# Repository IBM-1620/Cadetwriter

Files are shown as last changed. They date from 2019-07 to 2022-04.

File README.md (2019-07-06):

# Cadetwriter
Developed as a by-product of the IBM 1620 Jr. project, the Cadetwriter is a general-purpose ASCII terminal.  It can be connected via RS-232 or USB to any mini, micro, mainframe, or replica computer as a terminal device.  A commercial quality IBM/Lexmark Wheelwriter 1000 was adapted by interposing a circuit board containing a Teensy 3.5 microcontroller between the typewriter's keyboard and motherboard.  Custom firmware controls the typewriter and communicates with the host computer.  To support the full ASCII character set, characters not on the printwheel are synthesized using overprinted characters and "period graphics".  The Cadetwriter can print up to 16cps and is a reliable, low-maintenance, low-cost substitute for Teletype, DECwriter, Diablo, Spinwriter, Imagewriter, etc. teleprinters.

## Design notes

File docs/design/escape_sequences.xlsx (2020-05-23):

Cadetwriter Escape Sequence Recognition
Type | Escape (1 char) | Opener (1 char) | Parameters (0 - n chars) | Intermediates (0 - n chars) | Final (1 char)
CSI | <esc> 0x1B | [ 0x5B | 0123456789:;<=>? 0x30 - 0x3F | <space>!"#$%&'()*+,-./ 0x20 - 0x2F | @ABCDEFGHIJKLMNOPQRSTUVWXYZ[\]^_ `abcdefghijklmnopqrstuvwxyz{|}~ 0x40 - 0x7E
Function | <esc> 0x1B |  |  | <space>!"#$%&'()*+,-./ 0x20 - 0x2F | 0123456789:;<=>? @ABCDEFGHIJKLMNOPQRSTUVWXYZ[\]^_ `abcdefghijklmnopqrstuvwxyz{|}~ 0x30 - 0x7E
Type | Escape (1 char) | Opener (1 char) | Strings (0 - n chars) |  | Final (1 char)
String | <esc> 0x1B | PX]^_ 0x50, 0x58, 0x5D, 0x5E, 0x5F | <bs><tab><lf><vt><ff><cr> <space>!"#$%&'()*+,-./0123456789:;<=>? @ABCDEFGHIJKLMNOPQRSTUVWXYZ[\]^_ `abcdefghijklmnopqrstuvwxyz{|}~ 0x08 - 0x0D, 0x20 - 0x7E |  | <esc> \ 0x1B & 0x5C <bel> 0x07
Special cases:
 | NUL (0x00) and DEL (0x7F) are always ignored.
 | CAN (0x18) and SUB (0x1A) immediately abort the sequence.
 | All control characters (0x01 - 0x1F) except CAN (0x18), SUB (0x1A), and ESC (0x1B) anywhere, except in String bodies, perform their normal action.
 | P (0x50), X (0x58), ] (0x5D), ^ (0x5E), and _ (0x5F) cannot be used to terminate Function sequences unless they contain at least one Intermediate character.
 | Any ESC (0x1B) after the first, except in Strings, immediately aborts the current sequence and starts another one.

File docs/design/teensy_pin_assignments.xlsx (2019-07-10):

Teensy Pin Assignments
Pins | Port | Bit | I/O | Name | Firmware (1.7) | Firmware (2.0)
0 | B | 16 | I | RXD0, RX1 | UART_RX | UART_RX
1 | B | 17 | O | TXD0, TX1 | UART_TX | UART_TX
2 | D | 0 | I |  | ROW_IN_0 | ROW_IN_0
3 | A | 12 | I |  | COL_10 | COL_10
4 | A | 13 | I |  | COL_11 | COL_11
5 | D | 7 | I |  | ROW_IN_7 | ROW_IN_7
6 | D | 4 | I |  | ROW_IN_4 | ROW_IN_4
7 | D | 2 | I | RXD2, RX3 | ROW_IN_2 | ROW_IN_2
8 | D | 3 | I | TXD2, TX3 | ROW_IN_3 | ROW_IN_3
9 | C | 3 | I | RXD1, RX2 | COL_3 | COL_3
10 | C | 4 | I | TXD1, TX2, SS | COL_6 | COL_6
11 | C | 6 | I | MOSI | COL_7 | COL_7
12 | C | 7 | I | MISO | COL_8 | COL_8
13 | C | 5 | O | LED_BUILTIN | ORANGE_LED | ORANGE_LED
14 | D | 1 | I | ADC0, A0 | ROW_IN_1 | ROW_IN_1
15 | C | 0 | I | ADC1, A1 | COL_4 | COL_4
16 | B | 0 | O | ADC2, A2 | ROW_OUT_0 | ROW_OUT_0
17 | B | 1 | O | ADC3, A3 | ROW_OUT_1 | ROW_OUT_1
18 | B | 3 | O | ADC4, A4, SDA0, SDA | ROW_OUT_3 | SERIAL_CTSX
19 | B | 2 | O | ADC5, A5, SCL0, SCL | ROW_OUT_2 | SERIAL_RTSX
20 | D | 5 | I | ADC6, A6 | ROW_IN_5 | ROW_IN_5
21 | D | 6 | I | ADC7, A7 | ROW_IN_6 | ROW_IN_6
22 | C | 1 | I | ADC8, A8 | COL_14 | COL_14
23 | C | 2 | I | ADC9, A9 | COL_1 | COL_1
24 | E | 26 | I |  | JUMPER_6 | JUMPER_6
25 | A | 5 | I |  |  | COL_??
26 | A | 14 | I |  | COL_12 | COL_12
27 | A | 15 | I |  | COL_13 | COL_13
28 | A | 16 | I |  | COL_2 | COL_2
29 | B | 18 | O |  | ROW_OUT_6 | ROW_OUT_6
30 | B | 19 | O |  | ROW_OUT_7 | ROW_OUT_7
31 | B | 10 | O | ADC12, A12, RXD3, RX4 | ROW_OUT_4 | ROW_OUT_4
32 | B | 11 | O | ADC13, A13, TXD3, TX4 | ROW_OUT_5 | ROW_OUT_5
33 | E | 24 | O | ADC14, A14, TXD4, TX5 | BLUE_LED | BLUE_LED
34 | E | 25 | I | ADC15, A15, RXD4, RX5 | JUMPER_7 | JUMPER_7
35 | C | 8 | I | ADC16, A16 | COL_9 | COL_9
36 | C | 9 | O | ADC17, A17 | ROW_ENABLE | ROW_ENABLE
37 | C | 10 | O | ADC18, A18, SCL1 | SERIAL_RTS | ROW_OUT_2X
38 | C | 11 | I | ADC19, A19, SDA1 | SERIAL_CTS | ROW_OUT_3X
39 | A | 17 | I | ADC20, A20 | COL_5 | COL_5
40 | A | 28
41 | A | 29
42 | A | 26
43 | B | 20
44 | B | 22
45 | B | 23
46 | B | 21
47 | D | 8 |  | RX6
48 | D | 9 |  | TX6
49 | B | 4 |  | ADC23, A23
50 | B | 5 |  | ADC24, A24
51 | D | 14
52 | D | 13
53 | D | 12
54 | D | 15
55 | D | 11
56 | E | 10
57 | E | 11
58 | E | 0
59 | E | 1
60 | E | 2
61 | E | 3
62 | E | 4
63 | E | 5
64 |  |  |  | ADC10, A10
65 |  |  |  | ADC11, A11
66 |  |  |  | ADC21, A21, DAC0
67 |  |  |  | ADC22, A22, DAC1
68 |  |  |  | ADC25, A25
69 |  |  |  | ADC26, A26
 |  |  |  |  | input
 |  |  |  |  | output

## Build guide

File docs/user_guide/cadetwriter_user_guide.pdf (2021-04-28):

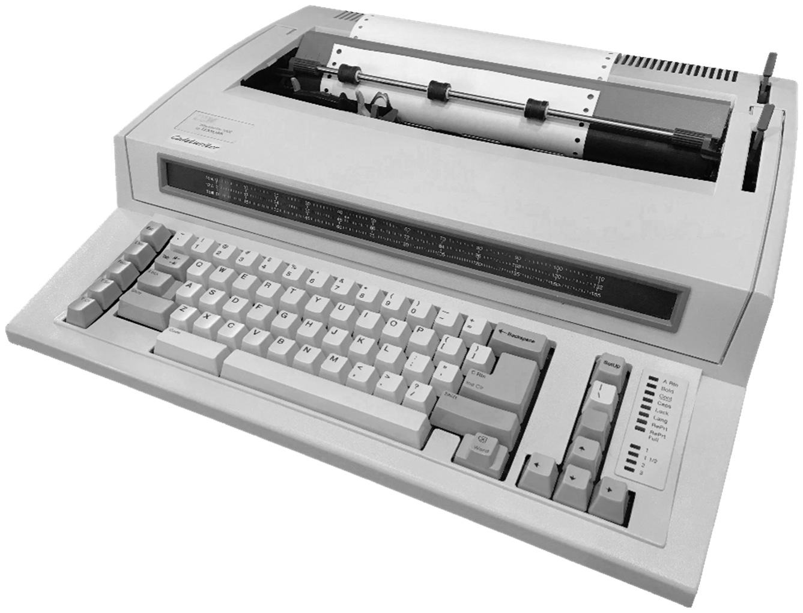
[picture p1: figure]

# Cadetwriter

# (ASCII Terminal)

# User Guide

### IBM 1620 Jr. Team Computer History Museum Revision 1.01 – April 2021

2

## Contents

3

4

## 1. Introduction

This guide describes the operation of Cadetwriter, a Wheelwriter‐based computer terminal. It is an extension of the console typewriter created for the Computer History Museum’s IBM 1620 Jr. project. Its complete design, assembly instructions, and firmware are available, free of charge from: https://github.com/IBM‐1620/Cadetwriter.

### 1.1 Description

Cadetwriter is a general‐purpose, ASCII computer teleprinter similar to a Teletype, DECwriter, Flexowriter, or IBM 2741 terminal. It can be used as an input/output device connected to any computer ‐ old, new, or replica ‐ with an RS‐232 or USB interface. It can also be operated as a stand‐alone typewriter by changing a hardware jumper.
Cadetwriter is built by installing a custom serial interface board inside an IBM/Lexmark Wheelwriter 1000 electronic typewriter.¹
Firmware in this
board’s ARM processor reads the keyboard, controls the printer, and communicates with the computer.

### 1.2 Features

Cadetwriter has the following features:

- Print speed up to 16 or 20 characters per second, depending on Wheelwriter model.
- 10, 12, or 15 pitch interchangeable typewheels, multiple fonts.²
- 80 ‐ 198 characters per line depending on printwheel pitch and carriage width.
- Standard and wide carriage widths.
- Full ASCII character set.
- RS‐232 and USB interfaces.
- Full or half duplex.
- Baud rates: 50, 75, 110, 134, 150, 200, 300, 600, 1200, 1800, 2400, 4800, 9600, 19200, 38400, 57600, 76800, 115200, or 230400.
- None, odd, or even parity.
- 7 or 8 data bits.

1 Although Cadetwriter was created using a Wheelwriter 1000, other model Wheelwriters also work with little or no change to the firmware or serial interface board. 2 Cadetwriter output is optimized for the Courier 10 ASCII (#1353909) and

Artisan 10 (#1353520) printwheels.

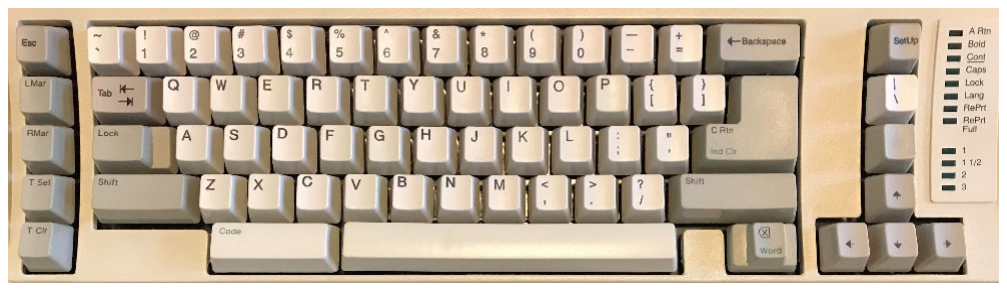
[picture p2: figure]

5

- 1 or 2 stop bits.
- Hardware (RTS/CTS or RTR/CTS) and/or software (XON/XOFF) flow control.
- Uppercase/lowercase or uppercase only.
- End‐of‐line: CR, LF, CR/LF, or LF/CR.
- Adjustable left and right margins.
- Settable tab stops.
- All settings are permanently retained.³

### 1.3 Keyboard

The Cadetwriter keyboard is as close to a typical ASCII terminal layout as possible with the Wheelwriter typewriter. In addition to printable characters, the keyboard includes keys to set/clear margins and tabs, move the carriage, and enter SetUp mode. The “Code” key functions as the “Ctrl” (control) key. This is Cadetwriter’s keyboard using replacement ASCII keycaps:

### 1.4 Printer

The printer in Cadetwriter is a Daisy wheel mechanism which prints fully‐ formed characters. Many printwheels exist for the Wheelwriter typewriter with different fonts, pitches, and foreign languages. Most of them contain a “typewriter” set of print characters which includes ½, ¼, ¢, ±, °, ², ³, §, and ¶. Missing are the ASCII characters <, >, \, ^, `, {, |, }, and ~.

IBM/Lexmark produced a limited number of special “ASCII” printwheels with all of the ASCII characters, but they are rare and hard to find. These are the preferred ones to use with Cadetwriter as they produce the best‐looking output and print at maximum speed. Here is Cadetwriter’s full character set when using the Courier 10 ASCII printwheel (#1353909):

3 Wheelwriter settings are stored in volatile memory, preserved by battery backup. All Cadetwriter setting are stored in non‐volatile EEPROM.

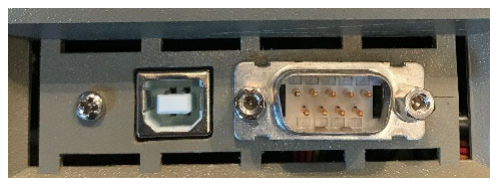
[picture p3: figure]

6

When using a standard, non‐ASCII printwheel, Cadetwriter synthesizes the missing characters by overprinting available characters, or “period graphic” characters⁴
, or a combination of the two methods. Composite characters, due to their complexity, take longer to print than the native ones, reducing the effective print speed. Here is the full ASCII character set as printed by Cadetwriter using the Artisan 10 printwheel (#1353520):

### 1.5 Indicator Lights

In normal operation, only the single‐spacing indicator light will be on. However, after printing several pages of output, the “RePrt Full” will light up, but will not affect the operation of the terminal.

The Shift Lock key on the keyboard functions as a caps lock, but the “Lock” indicator will not light up. This is due to the way Cadetwriter interfaces with the Wheelwriter electronics.

Note that when operating as a stand‐alone Wheelwriter typewriter, all of the indicator lights will have their standard meaning.

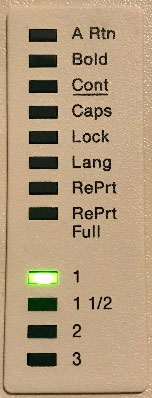
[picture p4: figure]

### 1.6 Serial Ports

Cadetwriter has two serial ports for connecting to a computer – RS‐232 and USB. The RS‐232 port is a male
DE‐9 (DTE) connector. The interface
uses RS‐232 voltages, not TTL level.
The USB port is a standard Type B receptable. Which port is used and its communication parameters are specified in the configuration settings [see section 2.2].

4 Period graphic characters are formed by a combination of micro‐space carriage movements (up, down, left, and right) and printing periods.

7

### The DE-9 pin assignments are:

Pin | Signal
1 | DCD – Data Carrier Detect †
2 | RXD – Received Data
3 | TXD – Transmitted Data
4 | DTR – Data Terminal Ready †
5 | GND – Common Ground
6 | DSR – Data Set Ready †
7 | RTS – Request To Send / RTR – Ready To Receive
8 | CTS – Clear To Send
9 | RI – Ring Indicator †

† DTR and DSR are not active and are connected together. DCD and RI are not connected.

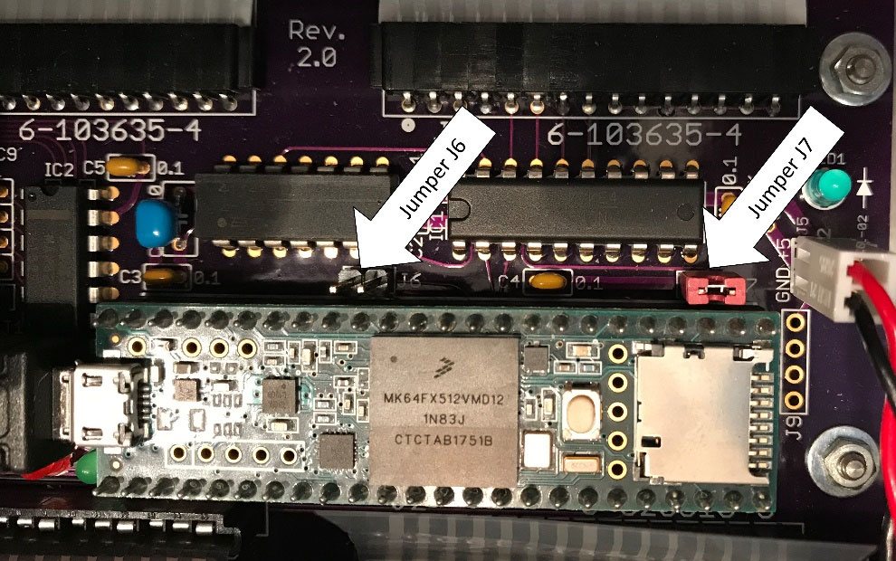
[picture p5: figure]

8

## 2. Setup

When connecting Cadetwriter to a computer for the first time, a little setup is required.

### 2.1 Selecting the Emulation

Four emulations are available by setting hardware jumpers on the serial interface board:

J6 Jumper | J7 Jumper | Emulation
| | IBM 1620 Jr. Console Typewriter
| installed | Cadetwriter ASCII Terminal
installed | | <available for future emulation>
installed | installed | Standalone Wheelwriter Typewriter
Here are the jumpers set to Cadetwriter ASCII Terminal emulation:

The emulation jumpers are tested only once when Cadetwriter is turned on. They can be changed when the device is off or on, but only take effect the next time it is turned on.

### 2.2 Batteries

It is recommended that you do NOT install batteries in Cadetwriter. When batteries are installed, it is possible for the Cadetwriter firmware to get out of sync with the typewriter settings, causing faulty operation. When batteries are not installed and the batteries installed configuration setting is

9

false, the firmware will set all typewriter settings to a known state at power on and operate correctly.

### 2.3 Configuring Cadetwriter

Most of the operations of Cadetwriter can be controlled by firmware configuration settings. These values are set interactively via a sequence of queries and controlled responses when in SetUp mode. The settings are effective for as long as Cadetwriter is turned on and can be optionally stored in EEPROM for persistence.

SetUp mode is entered by holding the “Code” and then pressing the “SetUp” key. The “SetUp” key is ignored if not used with the “Code” key. SetUp mode is not available when Cadetwriter is jumpered to be a standalone Wheelwriter typewriter.

While in SetUp mode, no data is sent to the computer and flow control (if enabled in settings) is asserted so that data should not be sent by the computer. If data is received, it will not be processed until SetUp mode is exited and may be lost if communication settings are changed.

SetUp mode starts by printing the following header which reports the emulation selected and the revision number of the firmware.

Next, the following command query is printed:

This illustrates the consistent way that SetUp mode queries commands and non‐typewriter settings:
- “Command” or the name of a specific setting (e.g., parity) is printed first.
- Next, all valid responses are shown inside brackets, separated by “/”s.⁵
- For commands, the default option is printed in all uppercase. All other possible commands are in lowercase.
- For settings, the current value [default] of the setting is printed in all uppercase. All other possible responses are in lowercase.

5 The exceptions are the baud rate, line length, and line offset settings which print the supported range of values and the current [default] value within the brackets. For example: “baud rate [50‐230400, 1200]”.

10

- The print mechanism spaces to the right so that the entire query is viewable.
- The user now enters a response to the query. Responses are case‐ insensitive. Only enough characters to uniquely specify a value need to be typed. In most cases, the first character is sufficient. If an invalid character is typed, nothing prints and the terminal beeps.
- Once enough characters are entered to uniquely identify the response, the remaining characters of it are printed and SetUp mode executes the command or updates the setting and moves on to the next one.
- When responding to the line length and line offset settings, a carriage return terminates the value.
- If only a carriage return is entered, then the default response is used. For commands, this exits SetUp mode. For settings, this retains the current value.
- At the end of all settings, SetUp mode asks if the new settings should be saved in EEPROM.

If “yes”, all settings are preserved until changed. If "no”, the new settings are in effect only as long as Cadetwriter remains turned on.

There are five commands:

settings ‐ Interactively review and optionally change all firmware configuration settings. See section 3 of this guide for details.

errors ‐ Print all errors and warnings that have occurred since the last power on or reset. Optionally, the error and warning counters can be cleared.

character set ‐ Print the full character set.

typewriter ‐ Set or clear all relevant typewriter settings. See section 4 of this guide for details.

quit ‐ End SetUp mode.

It is also possible to reset all firmware configuration settings to their “factory” default by pressing the “Shift”, “Code”, and “SetUp” keys together, aka Shift‐Ctrl‐SetUp. After resetting the settings, the firmware will re‐ establish all margins & tab stops and a confirmation message will be printed.

11

When using the RS‐232 serial port, the default settings are:

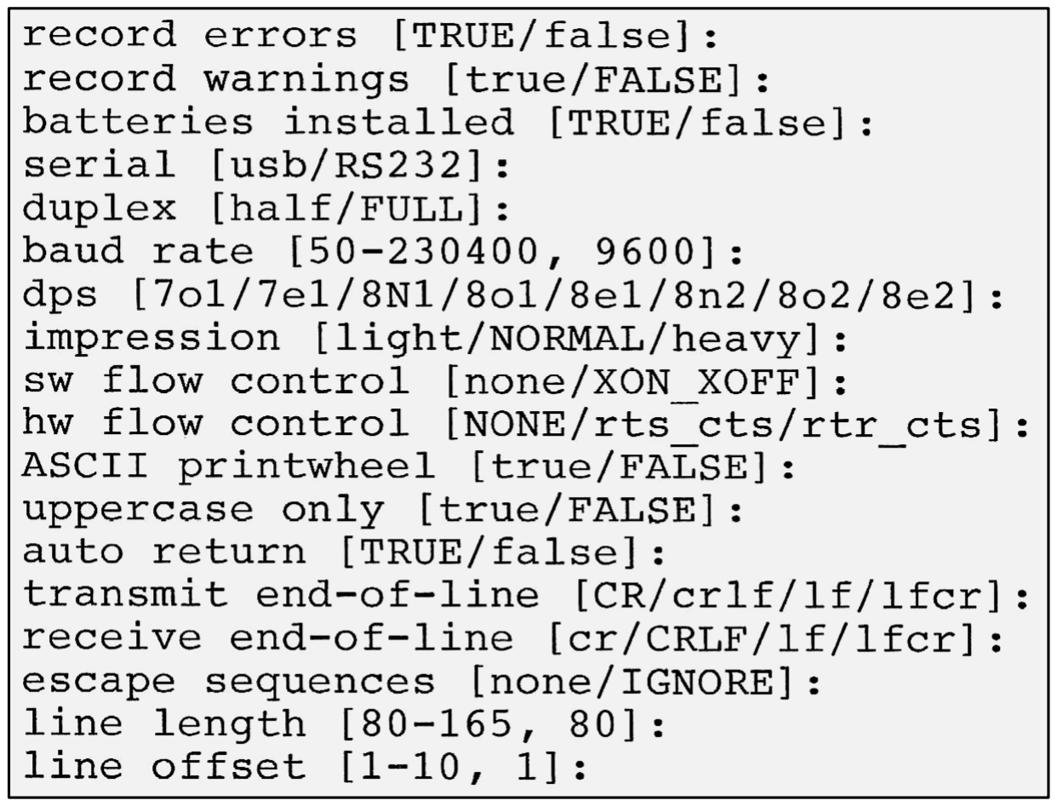
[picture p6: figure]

When using the USB serial port, the default settings are:

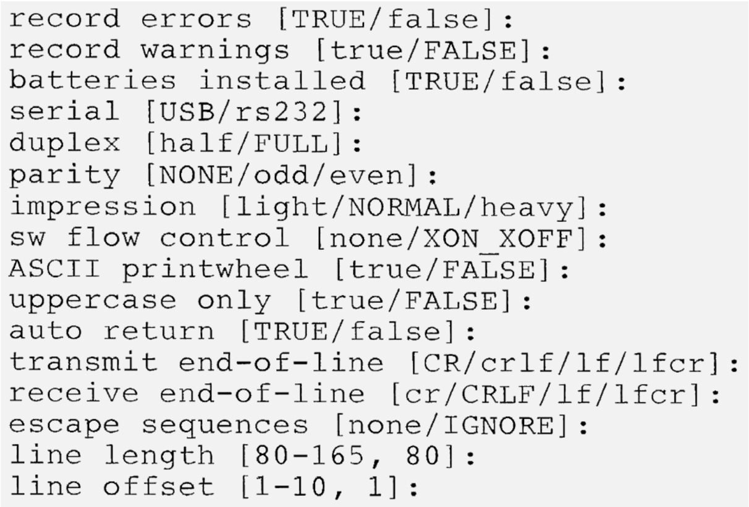
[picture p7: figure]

12

## 3. Configuration Settings

The firmware configuration settings are:

### 3.1 record errors

values: true, false
default: true
description: If “true”, keeps a count of internal errors and turns on the orange LED if an error occurs. If “false”, errors are not recorded.

### 3.2 record warnings

values: true, false
default: false
description: If “true”, keeps a count of internal warnings and turns on the blue LED if a warning occurs. If “false”, warnings are not recorded.

### 3.3 batteries installed

values: true, false
default: false
description: Notifies the firmware whether the Wheelwriter backup batteries are installed or not. If the value of this setting is not correct, there could be subtle terminal operational problems.

### 3.4 serial

values: usb, rs232
default: usb
description: Controls which serial communication port is used.

### 3.5 duplex

values: half, full
default: full
description: Controls whether Cadetwriter operates in full or half duplex.

### 3.6 parity

values: none, odd, even
default: none
description: Only applies when serial = usb. Controls the parity of transmitted characters. The parity of incoming characters is checked and generate a warning if incorrect. RS‐232 port parity is controlled by the dps setting.

13

### 3.7 baud rate

values: 50, 75, 110, 134, 150, 200, 300, 600, 1200, 1800, 2400, 4800, 9600, 19200, 38400, 57600, 76800, 115200, 230400
default: 9600
description: Only applies when serial = rs232.
Controls the baud rate of the RS‐232 serial communication port.

### 3.8 dps

values: 7o1, 7e1, 8n1, 8o1, 8e1, 8n2, 8o2, 8e2
default: 8n1
description: Only applies when serial = rs232. Controls the number of data bits, parity type, and number of stop bits of the RS‐232 serial communication port. These are the only useful combinations supported by the Cadetwriter serial interface hardware.

### 3.9 impression

values: light, normal, heavy
default: normal
description: Manages the typewriter’s impression control.

### 3.10 sw flow control

values: none, xon_xoff
default: xon_xoff
description: Controls whether software flow control is used with the selected serial communication port. Software flow control allows the user to type a Ctrl‐S (XOFF) to pause computer output and type a Ctrl‐Q (XON) to resume the output. The computer must support software flow control for this to work.

14

### 3.11 hw flow control

values: none, rts_cts, rtr_cts
default: none
description: Only applies when serial = rs232. Controls whether hardware flow control is used with the RS‐232 serial communication port. The difference between “rts_cts” and “rtr_cts” is the handling of the DE‐9 connector’s pin #7. In older RS‐232 specifications, pin #7 was RTS [Request To Send] which was used by the DTE [terminal] to request permission to send data to the DCE [computer]. As of the 1991 RS‐232‐E specification, RTS is assumed to always be asserted and pin #7 is now RTR [Ready To Receive] which the DTE uses to signal that it is able to receive data from the DCE. Pin #8 has always been CTS [Clear To Send] used to signal that the DTE can send data to the DCE. Many vendors incorrectly state their interface uses RTS when in fact it uses RTR. With true RTS, Cadetwriter cannot stop the computer from overwhelming it with data to print using hardware flow control.

### 3.12 ASCII printwheel

values: true, false
default: false
description: Indicates whether a specialized ASCII printwheel is installed. If “true”, native characters are used for all characters. If “false”, period graphic characters are used for the symbols missing from the printwheel.

### 3.13 uppercase only

values: true, false
default: false
description: Controls whether Cadetwriter transmits characters in uppercase only. This is equivalent to a permanent “Caps Lock”.

### 3.14 auto return

values: true, false
default: true
description: Controls what happens when a character arrives that would exceed the right margin. If “true”, a local carriage return is done. If “false”, characters stop printing and trigger beeps until a carriage return is received.

15

### 3.15 transmit end‐of‐line

values: cr, crlf, lf, lfcr
default: cr
description: Controls what character(s) are sent when the C Rtn key is pressed. Options include all combinations of carriage return [CR, Ctrl‐M] and/or line feed [LF, new line, NL, Ctrl‐J]. This option does not affect a manually typed Ctrl‐M or Ctrl‐J which is always sent as that single control character.

### 3.16 receive end‐of‐line

values: cr, crlf, lf, lfcr
default: crlf
description: Controls what character(s) trigger a local carriage return when received from the computer. Options include all combinations of carriage return [CR, Ctrl‐M] and/or line feed [LF, new line, NL, Ctrl‐J]. When a Ctrl‐M or Ctrl‐J character is received that is not part of a selected end‐of‐line combination, it performs the expected operation – Ctrl‐M returns the carriage without advancing the paper, Ctrl‐J advances the paper without returning the carriage.

### 3.17 escape sequences

values: none, ignore
default: ignore
description: Controls what happens when a recognized ANSI Escape Sequence is received. If none, escape sequences are treated as normal characters to be printed. If ignore, all recognized escape sequences are ignored.

### 3.18 line length

values: 80 ‐ 165 [198 for wide carriage] default: 80
description: Specifies the printable line length.

### 3.19 line offset

values: 1 ‐ 10
default: 1
description: Controls whether all printing is offset to the right by the specified number of columns. This must be at least 1 for period graphic special characters to print correctly in column 1. Some of the period graphic characters must micro‐space to the left of character‐center to print a period in the proper position.

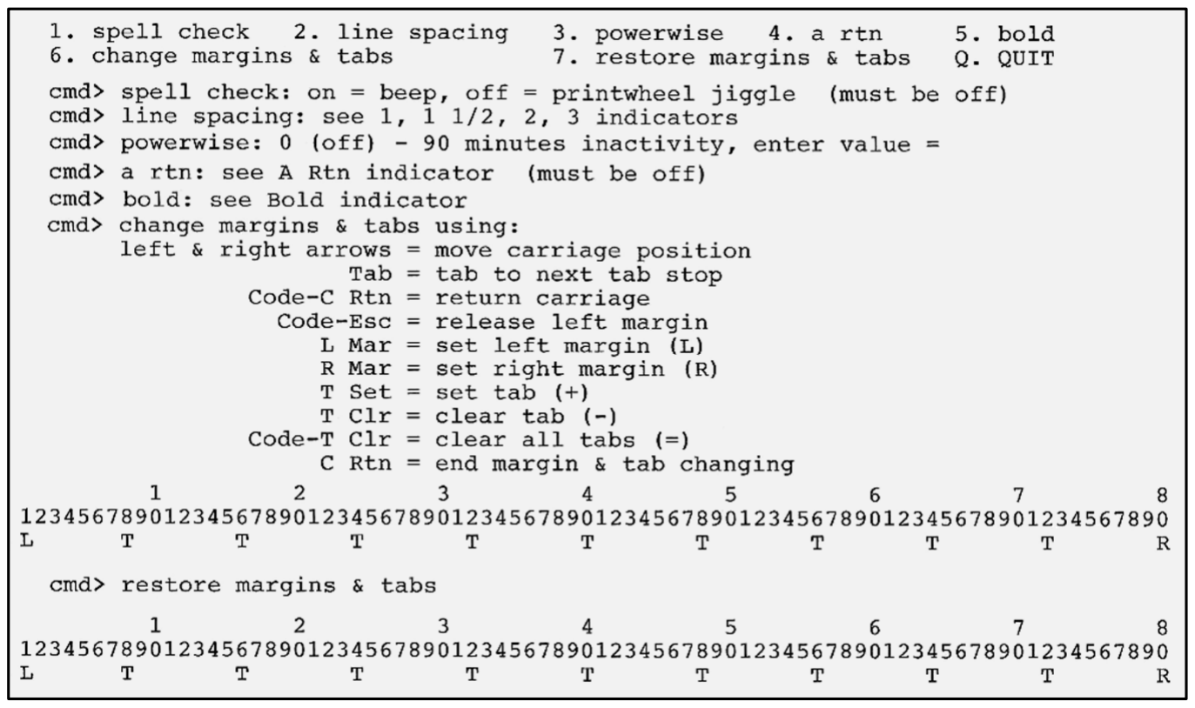
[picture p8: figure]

16

## 4. Typewriter Settings

The majority of the Wheelwriter settings don’t apply to Cadetwriter. Most of them are off when the typewriter is turned on, but spell check and A Rtn may be on and can cause operational problems. These settings are toggles and there is no way for the firmware to determine their current state, so the user must manually turn them off. This is done within the SetUp typewriter command by typing the associated index number (#1 for spell check and #4 for A Rtn), which toggles the setting.

There are three typewriter settings – line spacing, powerwise, and bold – which the user may find useful. Typing their index number will toggle the setting (#5 ‐ bold), sequence through the possible settings (#2 ‐ line spacing), or allow a value to be input (#3 ‐ powerwise).

Finally, there are two options in the typewriter setting’s menu for dealing with margins and tab stops. The restore option (#7) resets both margins and all tab stops to their “factory” default – left margin at column 1, right margin at the line length column, and tabs every 8 columns. The change option (#6) allows the user to interactively set the margins and tab stops by following the printed directions.

The typewriter settings available within SetUp mode are:

17

## 5. Operation

### 5.1 Powering On

When Cadetwriter is powered on, it performs a Power‐On Self‐Test (POST), restores all internal settings, flashes all of the indicator lights, resets the printwheel and ribbon, returns the carriage, beeps, moves over line offset spaces, and optionally sets all margins and tabs.

The POST reports firmware execution by turning on the orange LED when the startup code begins, turns off the orange LED when the startup code finishes and the main code begins, and blinks the blue LED for the first 5 seconds that keyboard scanning is occurring. After the POST, the orange and blue LEDs revert to indicating when an error or warning has occurred.

The margin / tab setting is done when the batteries installed setting is false or the hardware emulation jumpers have changed since the last power on. To set the margins and tabs, the carriage moves across the entire line and the printwheel spins as each margin and tab stop is set.

### 5.2 Using the Terminal

In general, Cadetwriter functions like any computer teleprinter. Here are the unique characteristics:
- Three keys (Code [Control], Esc, and | \) are in non‐standard locations.
- The key labelled Code is the Ctrl (control) key.
- The arrow keys on the lower‐right of the keyboard cause local carriage movement – up, down, left, right. Ctrl‐<up arrow> and Ctrl‐<down arrow> cause the carriage to roll up and down micro positions. Ctrl‐CRtn performs a local carriage return. No data is sent to the computer for any of these local carriage movements.
- The movement keys – up arrow, left arrow, down arrow, right arrow, space, and backspace – are auto‐repeating. If they are depressed for more than six seconds, they repeat at a 10 cps rate until released.
- The L Mar, R Mar, T Set, and T Clr keys on the left side of the keyboard are used to set/clear margins and tabs. These function locally and no data is sent to the computer. First, position the carriage to the desired position using the arrow keys, then press the appropriate key to set/clear a margin or a tab. The typewriter will respond with a beep or jiggling the printwheel. Margin and tab locations are preserved in the EEPROM.

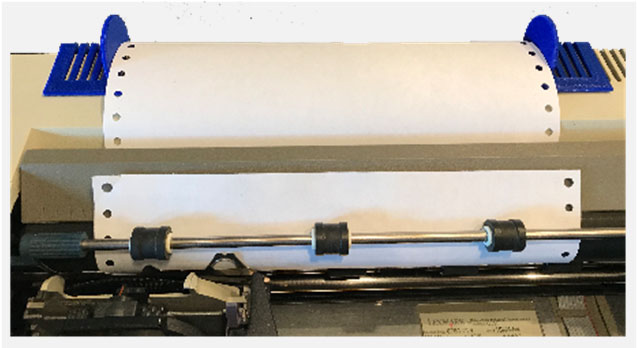
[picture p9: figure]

18

- Two special functions are available but not labelled on the keyboard:

Ctrl‐Esc – This operates as Margin Release. Press Ctrl‐Esc to allow moving left beyond the left margin. It only functions when the carriage is at the left margin.

Shift‐Ctrl‐SetUp – This resets all configuration settings to their “factory” value.
- Reviewing and/or changing firmware configuration settings is triggered by pressing Ctrl‐SetUp. See section 2.3 for more explanation.
- The Lock key is Caps Lock. It causes all alphabetic keys to be uppercase until a Shift key is pressed. The Lock indicator will not light.
- ASCII characters that are not on the installed printwheel have to be synthesized. They take longer to print, but printing will catch up with the subsequent characters. No characters will be lost.

### 5.3 Loading Paper

Shown with optional, add‐on paper guides.

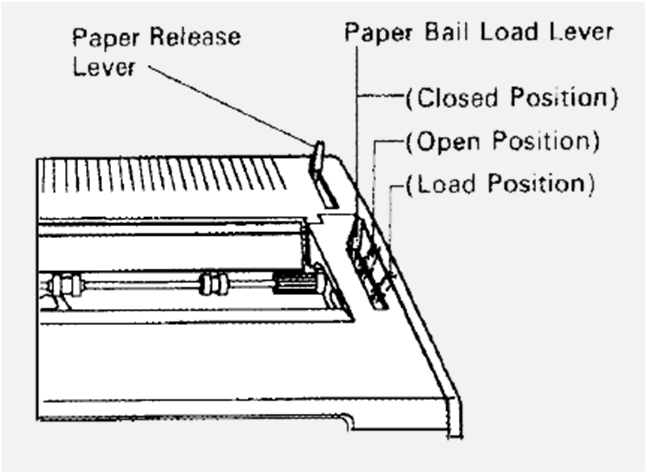
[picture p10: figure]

The steps to load paper are:
1. Turn on Cadetwriter if off.
2. Push the Paper Release Lever all the way back.
3. Place the paper in the terminal.
4. Pull the Paper Bail Load Lever to the load position. When the paper begins to feed, release the Paper Bail Load Lever.
5. Push the Paper Bail Load Lever back to the closed position.

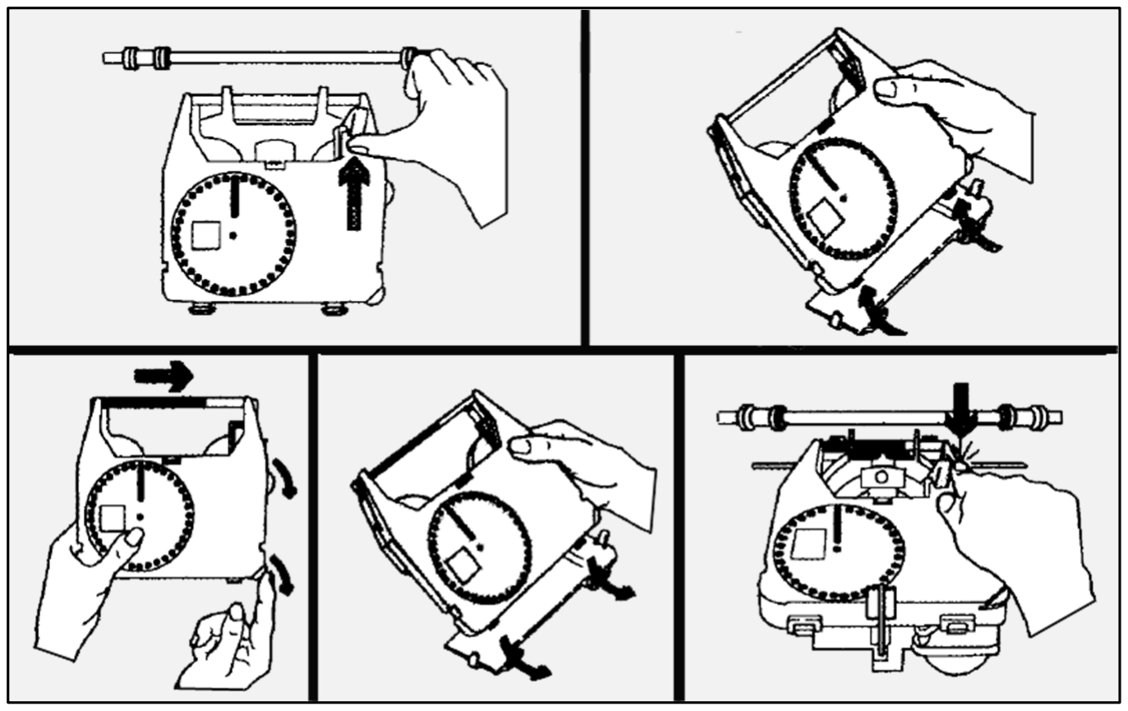
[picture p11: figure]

19

### 5.4 Replacing the Ribbon

The steps to replace the ribbon are:
1. Turn off Cadetwriter.
2. Push the blue lever to release the ribbon cassette.
3. Lift the ribbon cassette up and out.
4. Advance the ribbon on the new cassette to make it taut.
5. Slide the ribbon cassette into the typewriter.
6. Press down firmly on the ribbon cassette until it locks in place.
7. An attached correction ribbon won’t interfere, but is not used.

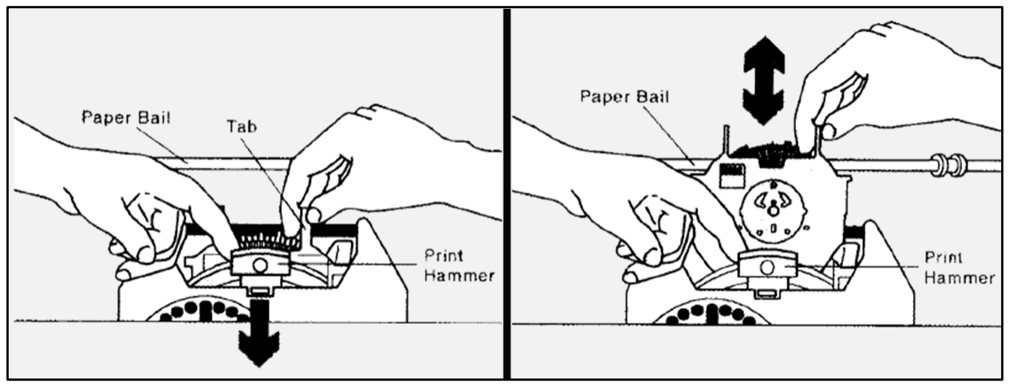
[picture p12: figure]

20

### 5.5 Replacing the Printwheel

The steps to replace the printwheel are:
1. Turn off Cadetwriter.
2. Pull the print hammer all the way forward and hold it.
3. Grasp the printwheel tab and lift the printwheel straight up and out of the slot.
4. Hold the new printwheel so the letters IBM are in the upper left corner.
5. Lower the printwheel into the slot. Make sure that it is fully seated.
6. Release the print hammer.

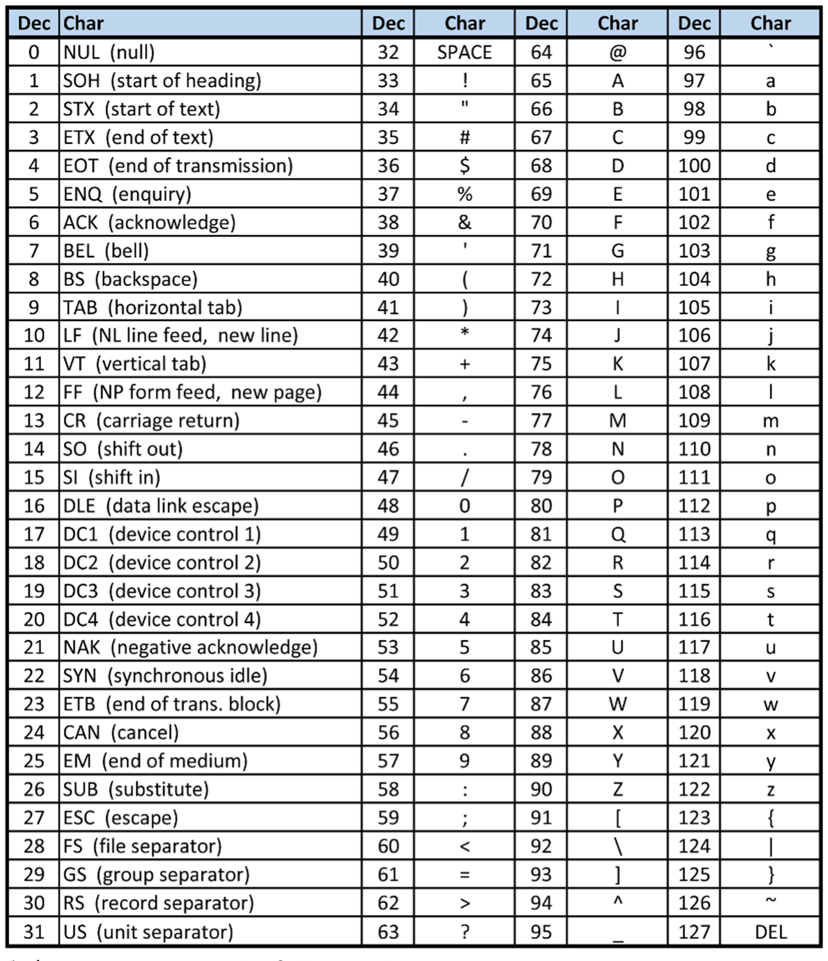
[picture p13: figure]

21

## A. ASCII Character Set

Cadetwriter supports the full ASCII character set.

22

Cadetwriter recognizes the full set of Escape Sequences defined by ISO/IEC 6429 (ECMA‐48, ANSI X3.64).

Escape (1 char) | Opener (1 char) | Parameters (0 ‐ n chars) | Intermediates (0 ‐ n chars) | Final (1 char)
<esc> 0x1B | [ 0x5B | 0123456789:;<=>? 0x30 ‐ 0x3F | <space>!"#$%&'() *+,‐./ 0x20 ‐ 0x2F | @ABCDEFGHIJKL MNOPQRSTUVWX YZ[\]^_ `abcdefghijklmnop qrstuvwxyz{|}~ 0x40 ‐ 0x7E
<esc> 0x1B | | | <space>!"#$%&'() *+,‐./ 0x20 ‐ 0x2F | 0123456789:;<=>? @ABCDEFGHIJKL MNOPQRSTUVWX YZ[\]^_ `abcdefghijklmnop qrstuvwxyz{|}~ 0x30 ‐ 0x7E
Escape (1 char) | Opener (1 char) | Strings (0 ‐ n chars) | | Final (1 char)
<esc> 0x1B | PX]^_ 0x50, 0x58, 0x5D, 0x5E, 0x5F | <bs><tab><lf><vt><ff><cr> <space>!"#$%&'()*+,‐ ./0123456789:;<=>? @ABCDEFGHIJKLMNOPQRSTUVWXYZ[\] ^_ `abcdefghijklmnopqrstuvwxyz{|}~ 0x08 ‐ 0x0D, 0x20 ‐ 0x7E | | <esc> \ 0x1B & 0x5C <bel> 0x07

There are special cases with escape sequences:
- NUL (0x00) and DEL (0x7F) are always ignored.
- CAN (0x18) and SUB (0x1A) immediately abort the sequence.
- All control characters (0x01 ‐ 0x1F) except CAN (0x18), SUB (0x1A), and ESC (0x1B) anywhere, except in String bodies, perform their normal action.
- P (0x50), X (0x58), ] (0x5D), ^ (0x5E), and _ (0x5F) cannot be used to terminate Function sequences unless they contain at least one Intermediate character.
- Any ESC (0x1B) after the first, except in Strings, immediately aborts the current sequence and starts another one.

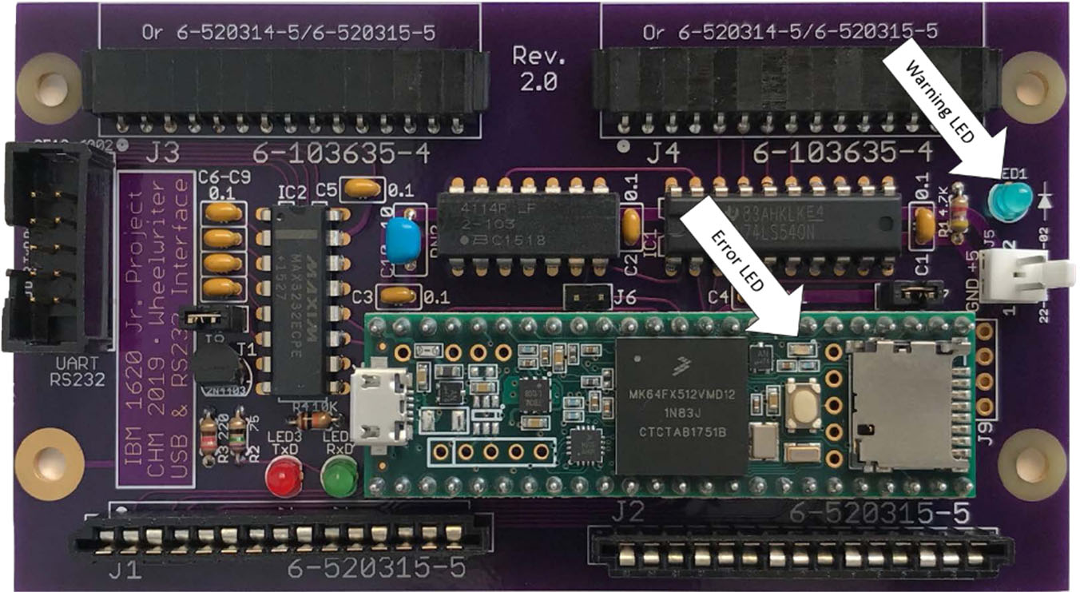
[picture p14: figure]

23

## B. Troubleshooting

Once Cadetwriter is set up and properly configured, it is a reliable computer terminal. However, there can be occasional problems, often caused by incorrect settings.

### B.1 Errors

The Cadetwriter firmware contains checks which can detect serious errors. If the record errors setting is true [the default is true], then any errors that occur will be counted and the orange Error LED will be turned on. All errors can cause the loss of data.

The SetUp mode “errors” command will print a list of any errors that have occurred with their counts. Optionally, the error counts can be cleared.

The possible errors are:

Error | Comments
Command buffer full | The internal command buffer is full. This could happen if the firmware’s main routine failed.
Receive buffer full | The internal receive buffer is full. This could happen if flow control is disabled or not working correctly.
Send buffer full | The internal send buffer is full. This could happen if flow control is disabled or not working correctly.
Transfer buffer full | The internal transfer buffer is full. This could happen if the firmware’s main routine failed.

24

Print buffer full | The internal print buffer is full. This could happen if the computer is flooding the terminal with data and flow control is either disabled or not working correctly.
Bad print code | An internal, predefined character string contains an invalid print code. This is a coding error in the firmware.
Bad escape sequence | An invalid escape sequence was received and the escape sequences setting is “ignore”. There is no way to properly handle sequences that do not follow the ISO/IEC 6429 standard, so it is possible that some sequence characters are erroneously printed or non‐sequence characters lost.
Bad element type | The type value in a character element is invalid. This is a coding error in the firmware.
Bad print spacing | The spacing value in a character element is invalid. This is a coding error in the firmware.
Bad printwheel position | The printwheel position value in a character element is invalid. This is a coding error in the firmware.
Bad key action | The action value in a key action table is invalid. This is a coding error in the firmware.
Bad serial action | The action value in a serial action table is invalid. This is a coding error in the firmware.

### B.2 Warnings

The Cadetwriter firmware contains checks which can detect minor unexpected conditions. If the record warnings setting is true [the default is false], then any warnings that occur will be counted and the blue Warning LED will be turned on. Warnings do not affect the correct functioning of
Cadetwriter.

The SetUp mode “errors” command will print a list of any warnings that have occurred with their counts. Optionally, the warning counts can be cleared.

The Wheelwriter motherboard controls the scanning of the keyboard. Most of the time, the [column] scans are in a consistent order and timing, but occasionally, they are not. The Cadetwriter firmware properly handles these abnormalities and no data is lost.

25

The possible warnings are:

Warning | Comments
Short column scan | A column scan was shorter than normal.
Long column scan | A column scan was longer than normal. This can be caused when too many synthesized characters are printed close together. When this happens, the terminal beeps 3 times and there can be a noticeable pause in printing.
Unexpected column scan | A column was scanned out‐of‐order.
Serial input incorrect parity | A character was received from the computer with incorrect parity.

### B.3 Problems

Listed below are some common problems and their explanations. Other typewriter‐specific problems and their solution can be found in the Wheelwriter User’s Guide.

### problem: The terminal is not communicating with the

computer.
solution: Communication problems have several causes.
- Is the correct port on the computer being used?
- Are the hardware jumpers [section 2.1] set to ASCII Terminal?
- Is the serial port setting [section 3] correct?
- If the RS‐232 port is selected, are the baud rate and dps settings [section 3] correct?
- If the RS‐232 port is being used, an incorrect [crossover aka null modem] cable might be the problem. Replace the cable with a straight‐thru one or add a null modem adapter.

problem: Typed characters do not print.
solution: If characters from the computer print, but keys typed on the keyboard don’t, that indicates a mismatch between the computer’s duplex setting and the terminal’s. The computer is set to half duplex and Cadetwriter is set to full duplex [section 3].

problem: Typed characters print twice.
solution: This happens when the computer is set to full duplex, but Cadetwriter is set to half duplex [section 3].

26

### problem: The carriage moves right and spins the printwheel

across the entire line.
solution: This is a normal behavior to set the margins and tab stops. It happens:
- Every time the terminal is turned on and the batteries installed setting [section 3] is false. If the batteries are really installed, correct the batteries installed setting.
- One time when the line length and/or line offset settings [section 3] are changed.
- One time when the terminal is turned on after the hardware emulation jumpers were changed.

problem: The terminal beeps a lot.
solution: There are many reasons that the terminal beeps:
- A single beep happens when a Ctrl‐G [BEL, 0x07] is received from the computer.
- A single beep happens when the carriage is five spaces from the right margin.
- A double beep happens when the Wheelwriter’s spell checker detects a word not in its dictionaries. Cadetwriter is designed to operate with the spell checker off. When the batteries installed setting isn’t correct, the Cadetwriter firmware and the Wheelwriter can get out‐of‐sync. Correct the batteries installed setting. The SetUp mode’s typewriter command #1 can be used to turn the spell check feature off.
- A triple beep and all of the line spacing lights are blinking happens when there is a problem with the Wheelwriter’s batteries. Turn off the terminal and replace the batteries.
- A triple beep with no blinking lights happens when the Wheelwriter’s input buffer is getting full. This can sometimes occur when the computer sends a large volume of output to be printed. This is not an error condition and all characters will print correctly with none lost.
- Six beeps and one or more lights blinking happens when the printwheel and/or ribbon are installed incorrectly. Turn off the terminal and reinstall the printwheel and ribbon.

problem: Some characters are not printed correctly.
solution: There are many different size, font, and language printwheels available. Cadetwriter was designed to use the Courier 10 ASCII (#1353909) or Artisan 10 (#1353520) printwheels. Use the correct printwheel.

27

### problem: Composite characters (<, >, \, ^, `, {, |, }, ~) don’t print

correctly in column 1.
solution: Most of the composite characters need to micro‐space to the left of character‐center to print a period. Physical column 1 of the Wheelwriter is up against a mechanical stop and the carriage cannot move to the left. Make sure that the line offset setting is at least 1.

problem: Lines are overprinting or double spacing.
solution: This happens when the Cadetwriter transmit end‐of‐line and/or receive end‐of‐line settings don’t match what the computer is using. Correct the end‐of‐line settings.

### problem: The carriage isn’t automatically or consistently

returned when the right margin is hit.
solution: This can happen when the auto return setting in SetUp mode is “false”. It should normally be set to “true”. An irregular automatic carriage return can happen when the Wheelwriter’s
A Rtn setting is on. If the “A Rtn” indicator is on, then turn off the setting using SetUp mode’s typewriter command #4.

### problem: Printed characters are not spaced evenly or the

carriage doesn’t return all the way.
solution: This is a mechanical issue with the Wheelwriter. Lubricating the guide rails will often correct the problem.

problem: The “RePrt Full” light comes on.
solution: The Wheelwriter stores all output in an internal print buffer to allow the user to re‐print pages (when used as a standalone typewriter). When the buffer is full, the “RePrt Full” light is turned on. Cadetwriter doesn’t use this feature and has no way to turn it off. It does not affect correct operation and can be safely ignored.

### problem: The “Lock” light does not turn on when the “Lock”

key is pressed.
solution: This is expected ‐ keyed alphabetic characters will be properly treated as uppercase, the light just won’t be on. It is a limitation caused by how the Cadetwriter serial interface board is connected to the Wheelwriter.

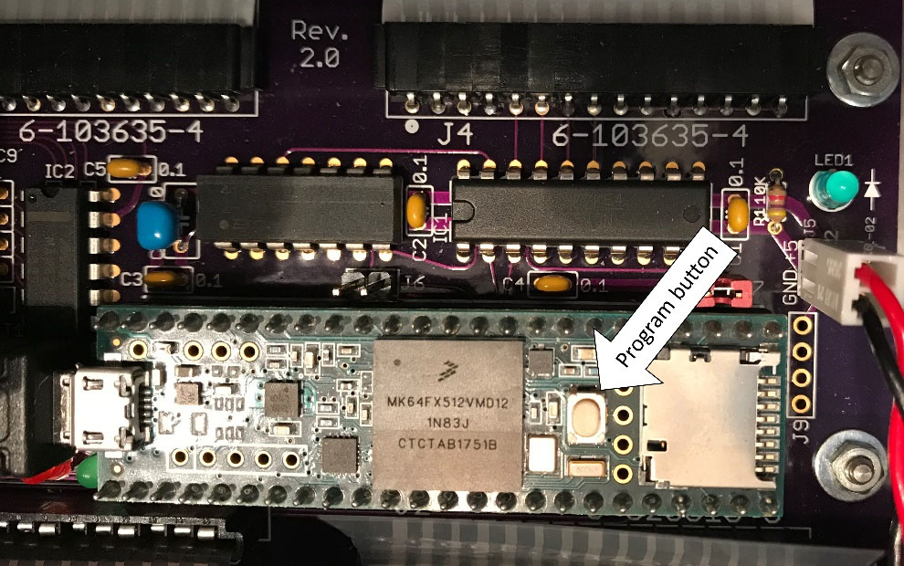
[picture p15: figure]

28

## C. Updating Firmware

In normal operation, there is no need to update the firmware in Cadetwriter. However, it is easy to install new firmware when it is needed to get a new feature or a bug fix.

The steps to update the firmware are:

1. Download the operating‐system‐specific Teensyduino Hex Loader from: https://www.pjrc.com/teensy/loader.html
2. Download the latest firmware hex binary from: https://github.com/IBM‐1620/Cadetwriter/blob/master/firmware/serial_interface_board/Serial_Interface_Board.ino.TEENSY35.hex
3. Connect the Cadetwriter to the computer using a USB cable.
4. Turn on the Cadetwriter.
5. Run the downloaded Teensyduino Hex Loader and select “File ‐> Open HEX File” supplying the downloaded firmware hex binary.
6. It may be necessary to press the Program button on the Cadetwriter serial interface board if the load doesn’t start on its own.
7. Once the loading completes, turn the Cadetwriter off and back on.

It is also possible to modify the source code to add custom feature(s), but describing that is beyond the scope of this User Guide. Note that the Cadetwriter Principles of Operation are documented in the source code itself.

29

## D. Support

Cadetwriter was developed by the Computer History Museum’s IBM 1620 Jr. project team. It is being made available free of charge to computer hobbyists with no implied warranty or formal support. However, the team is interested in helping others be successful with Cadetwriter and will make a best‐effort attempt to help.
The primary source of information and help with Cadetwriter is a set of channels at: https://cadetwriter.slack.com. These include:
- Announcements – Updates to the firmware, build instructions, documents, etc. will be announced here.
- Building – Used by those building a Cadetwriter to exchange information.
- Description – Contains general information about Cadetwriter.
- Operating – Information and questions/answers about using Cadetwriter.
- Suggestions – A place to post and discuss suggestions for changes/enhancements to Cadetwriter.

All of the Cadetwriter technical documentation and files are freely available at: https://github.com/IBM‐1620/Cadetwriter. This is also the site to file bugs in Cadetwriter firmware or hardware.

Finally, questions and comments can be emailed to:
cadetwriter@ibm1620.org.

30

## E. References

Here is a useful set of references for Cadetwriter:

### E.1 Documentation

- Cadetwriter User Guide.
https://www.github.com/IBM‐1620/Cadetwriter/tree/master/docs/user_guide/cadetwriter_user_guide.pdfhttps://www.github.com/IBM‐1620/Cadetwriter/tree/master/docs/user_guide/cadetwriter_user_guide_booklet.pdf
- Cadetwriter user community.
https://cadetwriter.slack.com
- Cadetwriter technical documentation and files. https://www.github.com/IBM‐1620/cadetwriter
- IBM/Lexmark Wheelwriter 1000 User’s Guide, P/N 1419147, Form No. SA40‐0825‐00, July 1994.
https://www.github.com/IBM‐1620/Cadetwriter/blob/master/docs/wheelwriter/wheelwriter_1000_user_manual.pdf

### E.2 Hardware

- Cadetwriter Adaptation Guide. https://github.com/IBM‐1620/Cadetwriter/blob/master/docs/adaptation_guide/wheelwriter‐adaptation‐instructions.pdf
- Cadetwriter Serial Interface Board. https://www/github.com/IBM‐1620/Cadetwriter/tree/master/hardware

### E.3 Firmware

- Cadetwriter firmware source. https://www.github.com/IBM‐1620/Cadetwriter/blob/master/firmware/serial_interface_board/Serial_Interface_Board.ino
- Cadetwriter firmware hex binary. https://www.github.com/IBM‐1620/Cadetwriter/blob/master/firmware/serial_interface_board/Serial_Interface_Board.ino.TEENSY35.hex
- SlowSoftSerial library.
https://www.github.com/MustBeArt/SlowSoftSerial
- Teensyduino Hex Loader.
https://www.pjrc.com/teensy/loader.html

31

- Arduino IDE.
https://www.arduino.cc/en/Main/Software
- Teensyduino IDE.
https://www.pjrc.com/teensy/td_download.html

### E.4 Accessories

- Optional paper guide:
https://www.thingiverse.com/thing:4079509

### E.5 Supplies

- IBM/Lexmark Courier 10 ASCII printwheel, IBM/Lexmark P/N 1353909. https://www.aroundtheoffice.com/IBM‐Printwheel‐Courier‐10‐1353909/productinfo/PW‐IBM‐1353909https://www.amazon.com/gp/product/B01IIIIVYW/ref=ppx_yo_dt_b_asin_title_o03_s00?ie=UTF8&psc=1
- IBM/Lexmark Artisan 10 printwheel, IBM/Lexmark P/N 1353520. https://www.aroundtheoffice.com/IBM‐Printwheel‐Artisan‐10‐1353520/productinfo/PW‐IBM‐1353520https://www.ibmtypewriters.com/type.html
- IBM/Lexmark ribbon, IBM/Lexmark P/N 1380999. https://www.staples.com/Wheelwriter‐Systems‐IBM‐Superior‐Write‐Correctable‐Film‐Ribbon‐model‐1380999/product_140111
- Fanfold 9.5” x 11” printer paper. https://www.staples.com/Staples‐Blank‐White‐Computer‐Paper‐Ultra‐Perforated‐20‐lb‐9‐1‐2‐x‐11‐1‐000‐Box/product_177089https://www.staples.com/Staples‐Computer‐Paper‐Ultra‐Perforated‐9‐1‐2‐x‐11‐Blank‐White‐20lb‐2‐500‐Box/product_177154

### E.6 Sales and Parts

- Batchelor Business Machines https://www.ibmtypewriters.com/
- Around the Office
https://www.aroundtheoffice.com/
- Typewriters.com
https://www.typewriters.com/

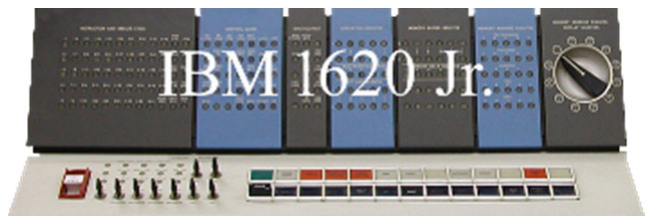
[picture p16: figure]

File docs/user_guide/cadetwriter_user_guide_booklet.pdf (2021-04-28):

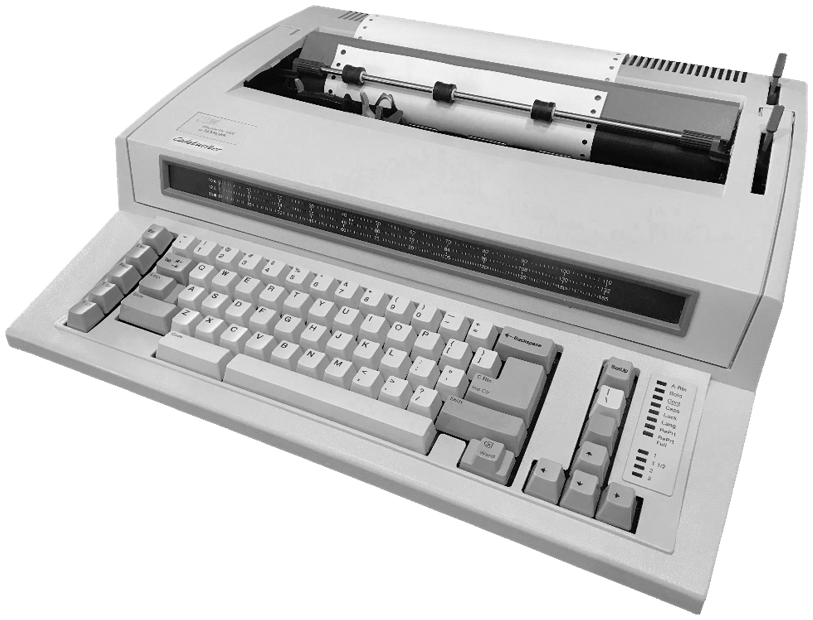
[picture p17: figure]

# Cadetwriter

# (ASCII Terminal)

# User Guide

### IBM 1620 Jr. Team Computer History Museum Revision 1.01 – April 2021


## Contents

- Arduino IDE.
https://www.arduino.cc/en/Main/Software
- Teensyduino IDE.
https://www.pjrc.com/teensy/td_download.html

### E.4 Accessories

- Optional paper guide:
https://www.thingiverse.com/thing:4079509

### E.5 Supplies

- IBM/Lexmark Courier 10 ASCII printwheel, IBM/Lexmark P/N 1353909. https://www.aroundtheoffice.com/IBM‐Printwheel‐Courier‐10‐1353909/productinfo/PW‐IBM‐1353909https://www.amazon.com/gp/product/B01IIIIVYW/ref=ppx_yo_dt_b_asin_title_o03_s00?ie=UTF8&psc=1
- IBM/Lexmark Artisan 10 printwheel, IBM/Lexmark P/N 1353520. https://www.aroundtheoffice.com/IBM‐Printwheel‐Artisan‐10‐1353520/productinfo/PW‐IBM‐1353520https://www.ibmtypewriters.com/type.html
- IBM/Lexmark ribbon, IBM/Lexmark P/N 1380999. https://www.staples.com/Wheelwriter‐Systems‐IBM‐Superior‐Write‐Correctable‐Film‐Ribbon‐model‐1380999/product_140111
- Fanfold 9.5” x 11” printer paper. https://www.staples.com/Staples‐Blank‐White‐Computer‐Paper‐Ultra‐Perforated‐20‐lb‐9‐1‐2‐x‐11‐1‐000‐Box/product_177089https://www.staples.com/Staples‐Computer‐Paper‐Ultra‐Perforated‐9‐1‐2‐x‐11‐Blank‐White‐20lb‐2‐500‐Box/product_177154

### E.6 Sales and Parts

- Batchelor Business Machines https://www.ibmtypewriters.com/
- Around the Office
https://www.aroundtheoffice.com/
- Typewriters.com
https://www.typewriters.com/

## E. References

Here is a useful set of references for Cadetwriter:

### E.1 Documentation

- Cadetwriter User Guide.
https://www.github.com/IBM‐1620/Cadetwriter/tree/master/docs/user_guide/cadetwriter_user_guide.pdfhttps://www.github.com/IBM‐1620/Cadetwriter/tree/master/docs/user_guide/cadetwriter_user_guide_booklet.pdf
- Cadetwriter user community.
https://cadetwriter.slack.com
- Cadetwriter technical documentation and files. https://www.github.com/IBM‐1620/cadetwriter
- IBM/Lexmark Wheelwriter 1000 User’s Guide, P/N 1419147, Form No. SA40‐0825‐00, July 1994.
https://www.github.com/IBM‐1620/Cadetwriter/blob/master/docs/wheelwriter/wheelwriter_1000_user_manual.pdf

### E.2 Hardware

- Cadetwriter Adaptation Guide. https://github.com/IBM‐1620/Cadetwriter/blob/master/docs/adaptation_guide/wheelwriter‐adaptation‐instructions.pdf
- Cadetwriter Serial Interface Board. https://www/github.com/IBM‐1620/Cadetwriter/tree/master/hardware

### E.3 Firmware

- Cadetwriter firmware source. https://www.github.com/IBM‐1620/Cadetwriter/blob/master/firmware/serial_interface_board/Serial_Interface_Board.ino
- Cadetwriter firmware hex binary. https://www.github.com/IBM‐1620/Cadetwriter/blob/master/firmware/serial_interface_board/Serial_Interface_Board.ino.TEENSY35.hex
- SlowSoftSerial library.
https://www.github.com/MustBeArt/SlowSoftSerial
- Teensyduino Hex Loader.
https://www.pjrc.com/teensy/loader.html
4. Typewriter Settings | 16
5. Operation | 17
5.1 Powering On | 17
5.2 Using the Terminal | 17
5.3 Loading Paper | 18
5.4 Replacing the Ribbon | 19
5.5 Replacing the Printwheel | 20
A. ASCII Character Set | 21
B. Troubleshooting | 23
B.1 Errors | 23
B.2 Warnings | 24
B.3 Problems | 25
C. Updating Firmware | 28
D. Support | 29
E. References | 30
E.1 Documentation | 30
E.2 Hardware | 30
E.3 Firmware | 30
E.4 Accessories | 31
E.5 Supplies | 31
E.6 Sales and Parts | 31

## 1. Introduction

This guide describes the operation of Cadetwriter, a Wheelwriter‐based computer terminal. It is an extension of the console typewriter created for the Computer History Museum’s IBM 1620 Jr. project. Its complete design, assembly instructions, and firmware are available, free of charge from: https://github.com/IBM‐1620/Cadetwriter.

### 1.1 Description

Cadetwriter is a general‐purpose, ASCII computer teleprinter similar to a Teletype, DECwriter, Flexowriter, or IBM 2741 terminal. It can be used as an input/output device connected to any computer ‐ old, new, or replica ‐ with an RS‐232 or USB interface. It can also be operated as a stand‐alone typewriter by changing a hardware jumper.
Cadetwriter is built by installing a custom serial interface board inside an IBM/Lexmark Wheelwriter 1000 electronic typewriter.¹ Firmware in this board’s ARM processor reads the keyboard, controls the printer, and communicates with the computer.

### 1.2 Features

Cadetwriter has the following features:

- Print speed up to 16 or 20 characters per second, depending on Wheelwriter model.
- 10, 12, or 15 pitch interchangeable typewheels, multiple fonts.²
- 80 ‐ 198 characters per line depending on printwheel pitch and carriage width.
- Standard and wide carriage widths.
- Full ASCII character set.
- RS‐232 and USB interfaces.
- Full or half duplex.
- Baud rates: 50, 75, 110, 134, 150, 200, 300, 600, 1200, 1800, 2400, 4800, 9600, 19200, 38400, 57600, 76800, 115200, or 230400.
- None, odd, or even parity.
- 7 or 8 data bits.

1 Although Cadetwriter was created using a Wheelwriter 1000, other model Wheelwriters also work with little or no change to the firmware or serial interface board.
2 Cadetwriter output is optimized for the Courier 10 ASCII (#1353909) and Artisan 10 (#1353520) printwheels.

## D. Support

Cadetwriter was developed by the Computer History Museum’s IBM 1620 Jr. project team. It is being made available free of charge to computer hobbyists with no implied warranty or formal support. However, the team is interested in helping others be successful with Cadetwriter and will make a best‐effort attempt to help.
The primary source of information and help with Cadetwriter is a set of channels at: https://cadetwriter.slack.com. These include:
- Announcements – Updates to the firmware, build instructions, documents, etc. will be announced here.
- Building – Used by those building a Cadetwriter to exchange information.
- Description – Contains general information about Cadetwriter.
- Operating – Information and questions/answers about using Cadetwriter.
- Suggestions – A place to post and discuss suggestions for changes/enhancements to Cadetwriter.

All of the Cadetwriter technical documentation and files are freely available at: https://github.com/IBM‐1620/Cadetwriter. This is also the site to file bugs in Cadetwriter firmware or hardware.

Finally, questions and comments can be emailed to:
cadetwriter@ibm1620.org.

## C. Updating Firmware

In normal operation, there is no need to update the firmware in Cadetwriter. However, it is easy to install new firmware when it is needed to get a new feature or a bug fix.

The steps to update the firmware are:

1. Download the operating‐system‐specific Teensyduino Hex Loader from: https://www.pjrc.com/teensy/loader.html
2. Download the latest firmware hex binary from: https://github.com/IBM‐1620/Cadetwriter/blob/master/firmware/serial_interface_board/Serial_Interface_Board.ino.TEENSY35.hex
3. Connect the Cadetwriter to the computer using a USB cable.
4. Turn on the Cadetwriter.
5. Run the downloaded Teensyduino Hex Loader and select “File ‐> Open HEX File” supplying the downloaded firmware hex binary.
6. It may be necessary to press the Program button on the Cadetwriter serial interface board if the load doesn’t start on its own.


7. Once the loading completes, turn the Cadetwriter off and back on.

It is also possible to modify the source code to add custom feature(s), but describing that is beyond the scope of this User Guide. Note that the Cadetwriter Principles of Operation are documented in the source code itself.

- 1 or 2 stop bits.
- Hardware (RTS/CTS or RTR/CTS) and/or software (XON/XOFF) flow control.
- Uppercase/lowercase or uppercase only.
- End‐of‐line: CR, LF, CR/LF, or LF/CR.
- Adjustable left and right margins.
- Settable tab stops.
- All settings are permanently retained.³

### 1.3 Keyboard

The Cadetwriter keyboard is as close to a typical ASCII terminal layout as possible with the Wheelwriter typewriter. In addition to printable characters, the keyboard includes keys to set/clear margins and tabs, move the carriage, and enter SetUp mode. The “Code” key functions as the “Ctrl” (control) key. This is Cadetwriter’s keyboard using replacement ASCII keycaps:


### 1.4 Printer

The printer in Cadetwriter is a Daisy wheel mechanism which prints fully‐ formed characters. Many printwheels exist for the Wheelwriter typewriter with different fonts, pitches, and foreign languages. Most of them contain a “typewriter” set of print characters which includes ½, ¼, ¢, ±, °, ², ³, §, and ¶. Missing are the ASCII characters <, >, \, ^, `, {, |, }, and ~.

IBM/Lexmark produced a limited number of special “ASCII” printwheels with all of the ASCII characters, but they are rare and hard to find. These are the preferred ones to use with Cadetwriter as they produce the best‐looking output and print at maximum speed. Here is Cadetwriter’s full character set when using the Courier 10 ASCII printwheel (#1353909):

3 Wheelwriter settings are stored in volatile memory, preserved by battery backup. All Cadetwriter setting are stored in non‐volatile EEPROM.

When using a standard, non‐ASCII printwheel, Cadetwriter synthesizes the missing characters by overprinting available characters, or “period graphic” characters⁴, or a combination of the two methods. Composite characters, due to their complexity, take longer to print than the native ones, reducing the effective print speed. Here is the full ASCII character set as printed by Cadetwriter using the Artisan 10 printwheel (#1353520):

### 1.5 Indicator Lights

In normal operation, only the single‐spacing indicator light will be on. However, after printing several pages of output, the “RePrt Full” will light up, but will not affect the operation of the terminal.

The Shift Lock key on the keyboard functions as a caps lock, but the “Lock” indicator will not light up. This is due to the way Cadetwriter interfaces with the Wheelwriter electronics.

Note that when operating as a stand‐alone Wheelwriter typewriter, all of the indicator lights will have their standard meaning.


### 1.6 Serial Ports

Cadetwriter has two serial ports for connecting to a computer – RS‐232 and USB. The RS‐232 port is a male
DE‐9 (DTE) connector. The interface
uses RS‐232 voltages, not TTL level.


The USB port is a standard Type B receptable. Which port is used and its communication parameters are specified in the configuration settings [see section 2.2].

4 Period graphic characters are formed by a combination of micro‐space carriage movements (up, down, left, and right) and printing periods.

### problem: Composite characters (<, >, \, ^, `, {, |, }, ~) don’t print

correctly in column 1.
solution: Most of the composite characters need to micro‐space to the left of character‐center to print a period. Physical column 1 of the Wheelwriter is up against a mechanical stop and the carriage cannot move to the left. Make sure that the line offset setting is at least 1.

problem: Lines are overprinting or double spacing.
solution: This happens when the Cadetwriter transmit end‐of‐line and/or receive end‐of‐line settings don’t match what the computer is using. Correct the end‐of‐line settings.

### problem: The carriage isn’t automatically or consistently

returned when the right margin is hit.
solution: This can happen when the auto return setting in SetUp mode is “false”. It should normally be set to “true”. An irregular automatic carriage return can happen when the Wheelwriter’s
A Rtn setting is on. If the “A Rtn” indicator is on, then turn off the setting using SetUp mode’s typewriter command #4.

### problem: Printed characters are not spaced evenly or the

carriage doesn’t return all the way.
solution: This is a mechanical issue with the Wheelwriter. Lubricating the guide rails will often correct the problem.

problem: The “RePrt Full” light comes on.
solution: The Wheelwriter stores all output in an internal print buffer to allow the user to re‐print pages (when used as a standalone typewriter). When the buffer is full, the “RePrt Full” light is turned on. Cadetwriter doesn’t use this feature and has no way to turn it off. It does not affect correct operation and can be safely ignored.

### problem: The “Lock” light does not turn on when the “Lock”

key is pressed.
solution: This is expected ‐ keyed alphabetic characters will be properly treated as uppercase, the light just won’t be on. It is a limitation caused by how the Cadetwriter serial interface board is connected to the Wheelwriter.

### problem: The carriage moves right and spins the printwheel

across the entire line.
solution: This is a normal behavior to set the margins and tab stops. It happens:
- Every time the terminal is turned on and the batteries installed setting [section 3] is false. If the batteries are really installed, correct the batteries installed setting.
- One time when the line length and/or line offset settings [section 3] are changed.
- One time when the terminal is turned on after the hardware emulation jumpers were changed.

problem: The terminal beeps a lot.
solution: There are many reasons that the terminal beeps:
- A single beep happens when a Ctrl‐G [BEL, 0x07] is received from the computer.
- A single beep happens when the carriage is five spaces from the right margin.
- A double beep happens when the Wheelwriter’s spell checker detects a word not in its dictionaries. Cadetwriter is designed to operate with the spell checker off. When the batteries installed setting isn’t correct, the Cadetwriter firmware and the Wheelwriter can get out‐of‐sync. Correct the batteries installed setting. The SetUp mode’s typewriter command #1 can be used to turn the spell check feature off.
- A triple beep and all of the line spacing lights are blinking happens when there is a problem with the Wheelwriter’s batteries. Turn off the terminal and replace the batteries.
- A triple beep with no blinking lights happens when the Wheelwriter’s input buffer is getting full. This can sometimes occur when the computer sends a large volume of output to be printed. This is not an error condition and all characters will print correctly with none lost.
- Six beeps and one or more lights blinking happens when the printwheel and/or ribbon are installed incorrectly. Turn off the terminal and reinstall the printwheel and ribbon.

problem: Some characters are not printed correctly.
solution: There are many different size, font, and language printwheels available. Cadetwriter was designed to use the Courier 10 ASCII (#1353909) or Artisan 10 (#1353520) printwheels. Use the correct printwheel.

### The DE-9 pin assignments are:

Pin | Signal
1 | DCD – Data Carrier Detect †
2 | RXD – Received Data
3 | TXD – Transmitted Data
4 | DTR – Data Terminal Ready †
5 | GND – Common Ground
6 | DSR – Data Set Ready †
7 | RTS – Request To Send / RTR – Ready To Receive
8 | CTS – Clear To Send
9 | RI – Ring Indicator †

† DTR and DSR are not active and are connected together. DCD and RI are not connected.

## 2. Setup

When connecting Cadetwriter to a computer for the first time, a little setup is required.

### 2.1 Selecting the Emulation

Four emulations are available by setting hardware jumpers on the serial interface board:

J6 Jumper | J7 Jumper | Emulation
| | IBM 1620 Jr. Console Typewriter
| installed | Cadetwriter ASCII Terminal
installed | | <available for future emulation>
installed | installed | Standalone Wheelwriter Typewriter
Here are the jumpers set to Cadetwriter ASCII Terminal emulation:


The emulation jumpers are tested only once when Cadetwriter is turned on. They can be changed when the device is off or on, but only take effect the next time it is turned on.

### 2.2 Batteries

It is recommended that you do NOT install batteries in Cadetwriter. When batteries are installed, it is possible for the Cadetwriter firmware to get out of sync with the typewriter settings, causing faulty operation. When batteries are not installed and the batteries installed configuration setting is

The possible warnings are:

Warning | Comments
Short column scan | A column scan was shorter than normal.
Long column scan | A column scan was longer than normal. This can be caused when too many synthesized characters are printed close together. When this happens, the terminal beeps 3 times and there can be a noticeable pause in printing.
Unexpected column scan | A column was scanned out‐of‐order.
Serial input incorrect parity | A character was received from the computer with incorrect parity.

### B.3 Problems

Listed below are some common problems and their explanations. Other typewriter‐specific problems and their solution can be found in the Wheelwriter User’s Guide.

### problem: The terminal is not communicating with the

computer.
solution: Communication problems have several causes.
- Is the correct port on the computer being used?
- Are the hardware jumpers [section 2.1] set to ASCII Terminal?
- Is the serial port setting [section 3] correct?
- If the RS‐232 port is selected, are the baud rate and dps settings [section 3] correct?
- If the RS‐232 port is being used, an incorrect [crossover aka null modem] cable might be the problem. Replace the cable with a straight‐thru one or add a null modem adapter.

problem: Typed characters do not print.
solution: If characters from the computer print, but keys typed on the keyboard don’t, that indicates a mismatch between the computer’s duplex setting and the terminal’s. The computer is set to half duplex and Cadetwriter is set to full duplex [section 3].

problem: Typed characters print twice.
solution: This happens when the computer is set to full duplex, but Cadetwriter is set to half duplex [section 3].

Print buffer full | The internal print buffer is full. This could happen if the computer is flooding the terminal with data and flow control is either disabled or not working correctly.
Bad print code | An internal, predefined character string contains an invalid print code. This is a coding error in the firmware.
Bad escape sequence | An invalid escape sequence was received and the escape sequences setting is “ignore”. There is no way to properly handle sequences that do not follow the ISO/IEC 6429 standard, so it is possible that some sequence characters are erroneously printed or non‐sequence characters lost.
Bad element type | The type value in a character element is invalid. This is a coding error in the firmware.
Bad print spacing | The spacing value in a character element is invalid. This is a coding error in the firmware.
Bad printwheel position | The printwheel position value in a character element is invalid. This is a coding error in the firmware.
Bad key action | The action value in a key action table is invalid. This is a coding error in the firmware.
Bad serial action | The action value in a serial action table is invalid. This is a coding error in the firmware.

### B.2 Warnings

The Cadetwriter firmware contains checks which can detect minor unexpected conditions. If the record warnings setting is true [the default is false], then any warnings that occur will be counted and the blue Warning LED will be turned on. Warnings do not affect the correct functioning of
Cadetwriter.

The SetUp mode “errors” command will print a list of any warnings that have occurred with their counts. Optionally, the warning counts can be cleared.

The Wheelwriter motherboard controls the scanning of the keyboard. Most of the time, the [column] scans are in a consistent order and timing, but occasionally, they are not. The Cadetwriter firmware properly handles these abnormalities and no data is lost.

false, the firmware will set all typewriter settings to a known state at power on and operate correctly.

### 2.3 Configuring Cadetwriter

Most of the operations of Cadetwriter can be controlled by firmware configuration settings. These values are set interactively via a sequence of queries and controlled responses when in SetUp mode. The settings are effective for as long as Cadetwriter is turned on and can be optionally stored in EEPROM for persistence.

SetUp mode is entered by holding the “Code” and then pressing the “SetUp” key. The “SetUp” key is ignored if not used with the “Code” key. SetUp mode is not available when Cadetwriter is jumpered to be a standalone Wheelwriter typewriter.

While in SetUp mode, no data is sent to the computer and flow control (if enabled in settings) is asserted so that data should not be sent by the computer. If data is received, it will not be processed until SetUp mode is exited and may be lost if communication settings are changed.

SetUp mode starts by printing the following header which reports the emulation selected and the revision number of the firmware.

Next, the following command query is printed:

This illustrates the consistent way that SetUp mode queries commands and non‐typewriter settings:
- “Command” or the name of a specific setting (e.g., parity) is printed first.
- Next, all valid responses are shown inside brackets, separated by “/”s.⁵
- For commands, the default option is printed in all uppercase. All other possible commands are in lowercase.
- For settings, the current value [default] of the setting is printed in all uppercase. All other possible responses are in lowercase.

5 The exceptions are the baud rate, line length, and line offset settings which print the supported range of values and the current [default] value within the brackets. For example: “baud rate [50‐230400, 1200]”.

- The print mechanism spaces to the right so that the entire query is viewable.
- The user now enters a response to the query. Responses are case‐ insensitive. Only enough characters to uniquely specify a value need to be typed. In most cases, the first character is sufficient. If an invalid character is typed, nothing prints and the terminal beeps.
- Once enough characters are entered to uniquely identify the response, the remaining characters of it are printed and SetUp mode executes the command or updates the setting and moves on to the next one.
- When responding to the line length and line offset settings, a carriage return terminates the value.
- If only a carriage return is entered, then the default response is used. For commands, this exits SetUp mode. For settings, this retains the current value.
- At the end of all settings, SetUp mode asks if the new settings should be saved in EEPROM.

If “yes”, all settings are preserved until changed. If "no”, the new settings are in effect only as long as Cadetwriter remains turned on.

There are five commands:

settings ‐ Interactively review and optionally change all firmware configuration settings. See section 3 of this guide for details.

errors ‐ Print all errors and warnings that have occurred since the last power on or reset. Optionally, the error and warning counters can be cleared.

character set ‐ Print the full character set.

typewriter ‐ Set or clear all relevant typewriter settings. See section 4 of this guide for details.

quit ‐ End SetUp mode.

It is also possible to reset all firmware configuration settings to their “factory” default by pressing the “Shift”, “Code”, and “SetUp” keys together, aka Shift‐Ctrl‐SetUp. After resetting the settings, the firmware will re‐ establish all margins & tab stops and a confirmation message will be printed.

## B. Troubleshooting

Once Cadetwriter is set up and properly configured, it is a reliable computer terminal. However, there can be occasional problems, often caused by incorrect settings.


### B.1 Errors

The Cadetwriter firmware contains checks which can detect serious errors. If the record errors setting is true [the default is true], then any errors that occur will be counted and the orange Error LED will be turned on. All errors can cause the loss of data.

The SetUp mode “errors” command will print a list of any errors that have occurred with their counts. Optionally, the error counts can be cleared.

The possible errors are:

Error | Comments
Command buffer full | The internal command buffer is full. This could happen if the firmware’s main routine failed.
Receive buffer full | The internal receive buffer is full. This could happen if flow control is disabled or not working correctly.
Send buffer full | The internal send buffer is full. This could happen if flow control is disabled or not working correctly.
Transfer buffer full | The internal transfer buffer is full. This could happen if the firmware’s main routine failed.

Cadetwriter recognizes the full set of Escape Sequences defined by ISO/IEC 6429 (ECMA‐48, ANSI X3.64).

Escape (1 char) | Opener (1 char) | Parameters (0 ‐ n chars) | Intermediates (0 ‐ n chars) | Final (1 char)
<esc> 0x1B | [ 0x5B | 0123456789:;<=>? 0x30 ‐ 0x3F | <space>!"#$%&'() *+,‐./ 0x20 ‐ 0x2F | @ABCDEFGHIJKL MNOPQRSTUVWX YZ[\]^_ `abcdefghijklmnop qrstuvwxyz{|}~ 0x40 ‐ 0x7E
<esc> 0x1B | | | <space>!"#$%&'() *+,‐./ 0x20 ‐ 0x2F | 0123456789:;<=>? @ABCDEFGHIJKL MNOPQRSTUVWX YZ[\]^_ `abcdefghijklmnop qrstuvwxyz{|}~ 0x30 ‐ 0x7E
Escape (1 char) | Opener (1 char) | Strings (0 ‐ n chars) | | Final (1 char)
<esc> 0x1B | PX]^_ 0x50, 0x58, 0x5D, 0x5E, 0x5F | <bs><tab><lf><vt><ff><cr> <space>!"#$%&'()*+,‐ ./0123456789:;<=>? @ABCDEFGHIJKLMNOPQRSTUVWXYZ[\] ^_ `abcdefghijklmnopqrstuvwxyz{|}~ 0x08 ‐ 0x0D, 0x20 ‐ 0x7E | | <esc> \ 0x1B & 0x5C <bel> 0x07


There are special cases with escape sequences:
- NUL (0x00) and DEL (0x7F) are always ignored.
- CAN (0x18) and SUB (0x1A) immediately abort the sequence.
- All control characters (0x01 ‐ 0x1F) except CAN (0x18), SUB (0x1A), and ESC (0x1B) anywhere, except in String bodies, perform their normal action.
- P (0x50), X (0x58), ] (0x5D), ^ (0x5E), and _ (0x5F) cannot be used to terminate Function sequences unless they contain at least one Intermediate character.
- Any ESC (0x1B) after the first, except in Strings, immediately aborts the current sequence and starts another one.

When using the RS‐232 serial port, the default settings are:

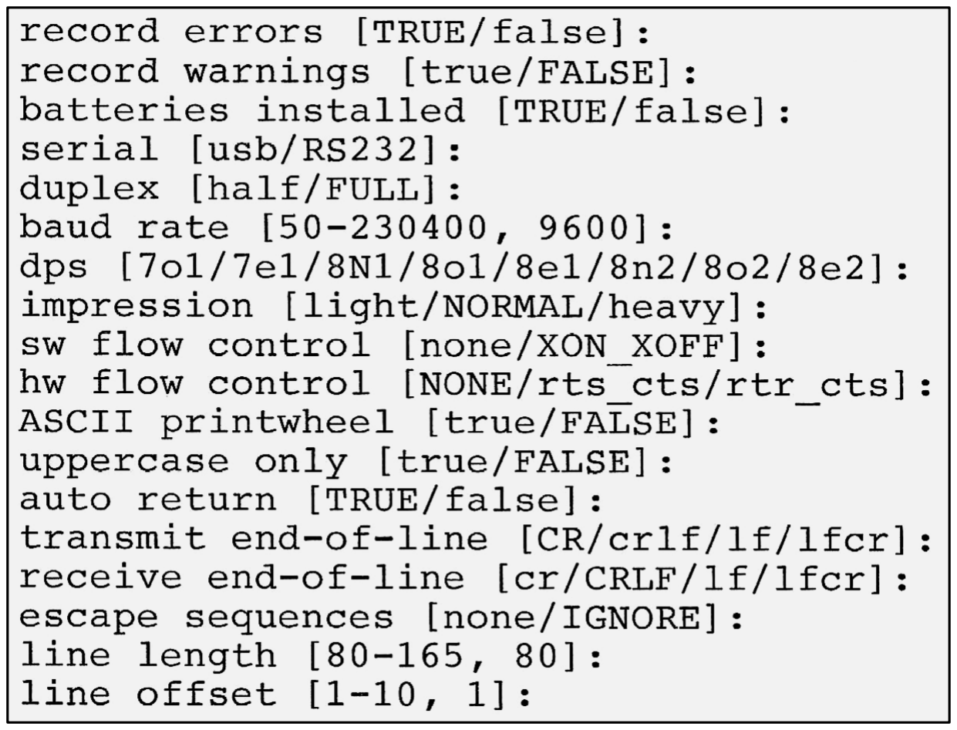
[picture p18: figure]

When using the USB serial port, the default settings are:

## 3. Configuration Settings

The firmware configuration settings are:

### 3.1 record errors

values: true, false
default: true
description: If “true”, keeps a count of internal errors and turns on the orange LED if an error occurs. If “false”, errors are not recorded.

### 3.2 record warnings

values: true, false
default: false
description: If “true”, keeps a count of internal warnings and turns on the blue LED if a warning occurs. If “false”, warnings are not recorded.

### 3.3 batteries installed

values: true, false
default: false
description: Notifies the firmware whether the Wheelwriter backup batteries are installed or not. If the value of this setting is not correct, there could be subtle terminal operational problems.

### 3.4 serial

values: usb, rs232
default: usb
description: Controls which serial communication port is used.

### 3.5 duplex

values: half, full
default: full
description: Controls whether Cadetwriter operates in full or half duplex.

### 3.6 parity

values: none, odd, even
default: none
description: Only applies when serial = usb. Controls the parity of transmitted characters. The parity of incoming characters is checked and generate a warning if incorrect. RS‐232 port parity is controlled by the dps setting.

## A. ASCII Character Set

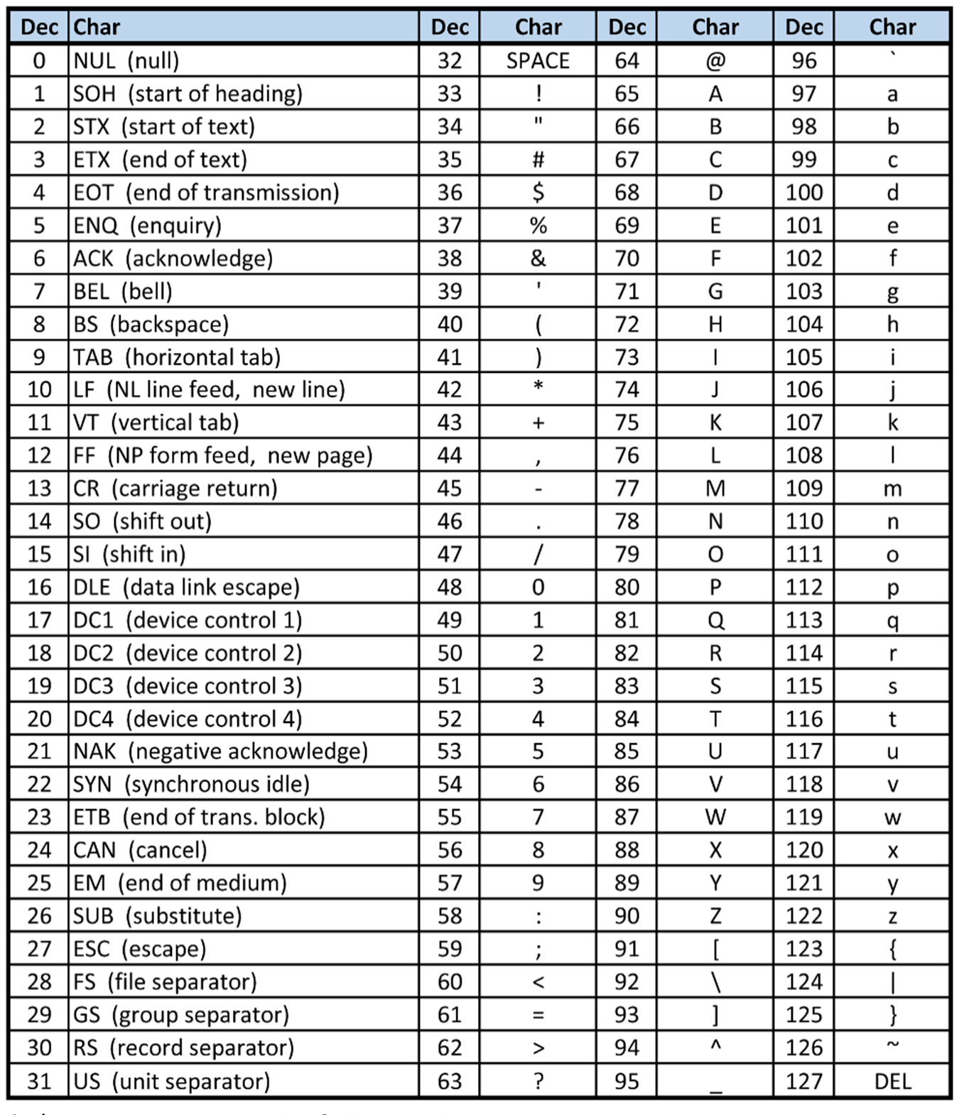
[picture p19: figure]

Cadetwriter supports the full ASCII character set.

### 5.5 Replacing the Printwheel

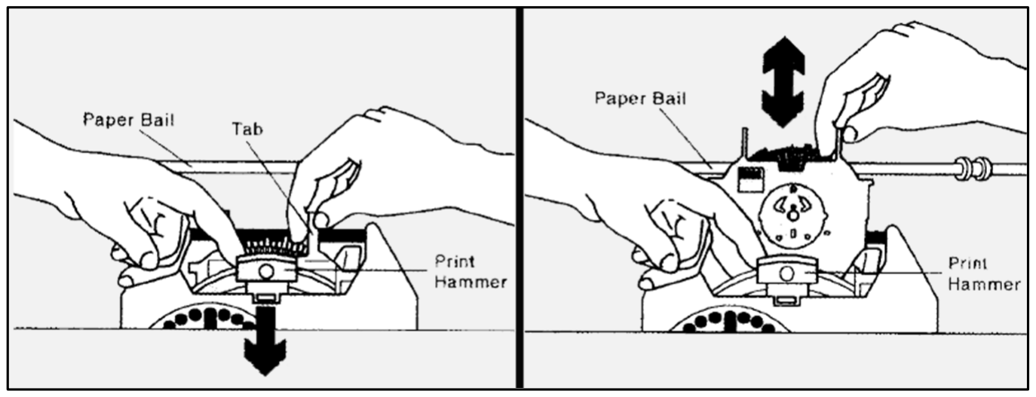
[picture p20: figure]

The steps to replace the printwheel are:
1. Turn off Cadetwriter.
2. Pull the print hammer all the way forward and hold it.
3. Grasp the printwheel tab and lift the printwheel straight up and out of the slot.
4. Hold the new printwheel so the letters IBM are in the upper left corner.
5. Lower the printwheel into the slot. Make sure that it is fully seated.
6. Release the print hammer.

### 3.7 baud rate

values: 50, 75, 110, 134, 150, 200, 300, 600, 1200, 1800, 2400, 4800, 9600, 19200, 38400, 57600, 76800, 115200, 230400
default: 9600
description: Only applies when serial = rs232.
Controls the baud rate of the RS‐232 serial communication port.

### 3.8 dps

values: 7o1, 7e1, 8n1, 8o1, 8e1, 8n2, 8o2, 8e2
default: 8n1
description: Only applies when serial = rs232. Controls the number of data bits, parity type, and number of stop bits of the RS‐232 serial communication port. These are the only useful combinations supported by the Cadetwriter serial interface hardware.

### 3.9 impression

values: light, normal, heavy
default: normal
description: Manages the typewriter’s impression control.

### 3.10 sw flow control

values: none, xon_xoff
default: xon_xoff
description: Controls whether software flow control is used with the selected serial communication port. Software flow control allows the user to type a Ctrl‐S (XOFF) to pause computer output and type a Ctrl‐Q (XON) to resume the output. The computer must support software flow control for this to work.

### 3.11 hw flow control

values: none, rts_cts, rtr_cts
default: none
description: Only applies when serial = rs232. Controls whether hardware flow control is used with the RS‐232 serial communication port. The difference between “rts_cts” and “rtr_cts” is the handling of the DE‐9 connector’s pin #7. In older RS‐232 specifications, pin #7 was RTS [Request To Send] which was used by the DTE [terminal] to request permission to send data to the DCE [computer]. As of the 1991 RS‐232‐E specification, RTS is assumed to always be asserted and pin #7 is now RTR [Ready To Receive] which the DTE uses to signal that it is able to receive data from the DCE. Pin #8 has always been CTS [Clear To Send] used to signal that the DTE can send data to the DCE. Many vendors incorrectly state their interface uses RTS when in fact it uses RTR. With true RTS, Cadetwriter cannot stop the computer from overwhelming it with data to print using hardware flow control.

### 3.12 ASCII printwheel

values: true, false
default: false
description: Indicates whether a specialized ASCII printwheel is installed. If “true”, native characters are used for all characters. If “false”, period graphic characters are used for the symbols missing from the printwheel.

### 3.13 uppercase only

values: true, false
default: false
description: Controls whether Cadetwriter transmits characters in uppercase only. This is equivalent to a permanent “Caps Lock”.

### 3.14 auto return

values: true, false
default: true
description: Controls what happens when a character arrives that would exceed the right margin. If “true”, a local carriage return is done. If “false”, characters stop printing and trigger beeps until a carriage return is received.

### 5.4 Replacing the Ribbon

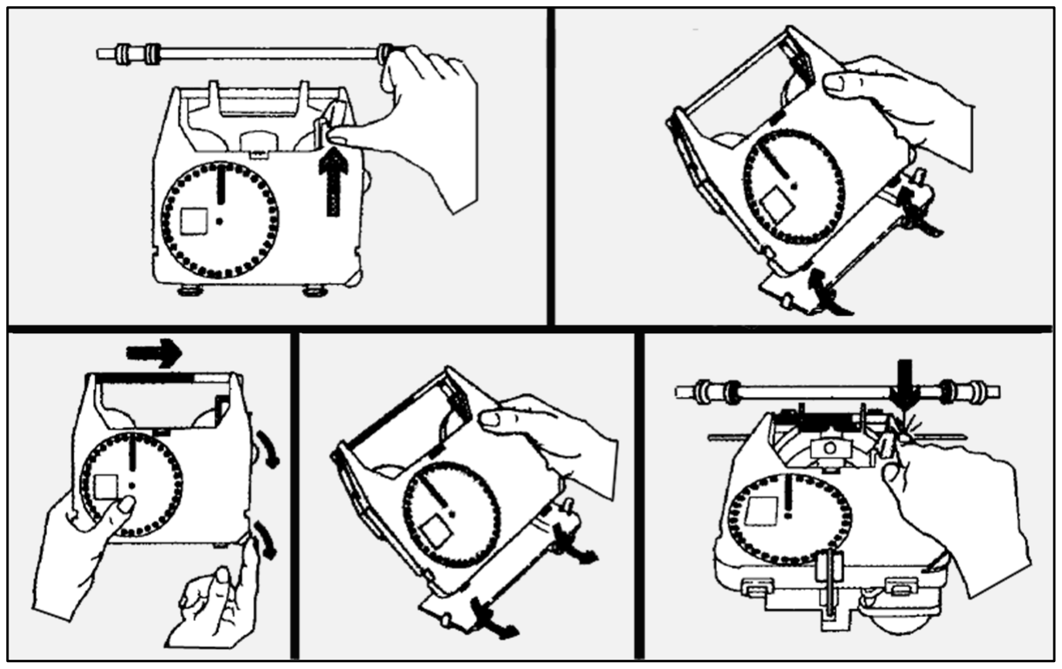
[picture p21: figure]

The steps to replace the ribbon are:
1. Turn off Cadetwriter.
2. Push the blue lever to release the ribbon cassette.
3. Lift the ribbon cassette up and out.
4. Advance the ribbon on the new cassette to make it taut.
5. Slide the ribbon cassette into the typewriter.
6. Press down firmly on the ribbon cassette until it locks in place.
7. An attached correction ribbon won’t interfere, but is not used.

- Two special functions are available but not labelled on the keyboard:

Ctrl‐Esc – This operates as Margin Release. Press Ctrl‐Esc to allow moving left beyond the left margin. It only functions when the carriage is at the left margin.

Shift‐Ctrl‐SetUp – This resets all configuration settings to their “factory” value.
- Reviewing and/or changing firmware configuration settings is triggered by pressing Ctrl‐SetUp. See section 2.3 for more explanation.
- The Lock key is Caps Lock. It causes all alphabetic keys to be uppercase until a Shift key is pressed. The Lock indicator will not light.
- ASCII characters that are not on the installed printwheel have to be synthesized. They take longer to print, but printing will catch up with the subsequent characters. No characters will be lost.

### 5.3 Loading Paper


Shown with optional, add‐on paper guides.


The steps to load paper are:
1. Turn on Cadetwriter if off.
2. Push the Paper Release Lever all the way back.
3. Place the paper in the terminal.
4. Pull the Paper Bail Load Lever to the load position. When the paper begins to feed, release the Paper Bail Load Lever.
5. Push the Paper Bail Load Lever back to the closed position.

### 3.15 transmit end‐of‐line

values: cr, crlf, lf, lfcr
default: cr
description: Controls what character(s) are sent when the C Rtn key is pressed. Options include all combinations of carriage return [CR, Ctrl‐M] and/or line feed [LF, new line, NL, Ctrl‐J]. This option does not affect a manually typed Ctrl‐M or Ctrl‐J which is always sent as that single control character.

### 3.16 receive end‐of‐line

values: cr, crlf, lf, lfcr
default: crlf
description: Controls what character(s) trigger a local carriage return when received from the computer. Options include all combinations of carriage return [CR, Ctrl‐M] and/or line feed [LF, new line, NL, Ctrl‐J]. When a Ctrl‐M or Ctrl‐J character is received that is not part of a selected end‐of‐line combination, it performs the expected operation – Ctrl‐M returns the carriage without advancing the paper, Ctrl‐J advances the paper without returning the carriage.

### 3.17 escape sequences

values: none, ignore
default: ignore
description: Controls what happens when a recognized ANSI Escape Sequence is received. If none, escape sequences are treated as normal characters to be printed. If ignore, all recognized escape sequences are ignored.

### 3.18 line length

values: 80 ‐ 165 [198 for wide carriage] default: 80
description: Specifies the printable line length.

### 3.19 line offset

values: 1 ‐ 10
default: 1
description: Controls whether all printing is offset to the right by the specified number of columns. This must be at least 1 for period graphic special characters to print correctly in column 1. Some of the period graphic characters must micro‐space to the left of character‐center to print a period in the proper position.

## 4. Typewriter Settings

The majority of the Wheelwriter settings don’t apply to Cadetwriter. Most of them are off when the typewriter is turned on, but spell check and A Rtn may be on and can cause operational problems. These settings are toggles and there is no way for the firmware to determine their current state, so the user must manually turn them off. This is done within the SetUp typewriter command by typing the associated index number (#1 for spell check and #4 for A Rtn), which toggles the setting.

There are three typewriter settings – line spacing, powerwise, and bold – which the user may find useful. Typing their index number will toggle the setting (#5 ‐ bold), sequence through the possible settings (#2 ‐ line spacing), or allow a value to be input (#3 ‐ powerwise).

Finally, there are two options in the typewriter setting’s menu for dealing with margins and tab stops. The restore option (#7) resets both margins and all tab stops to their “factory” default – left margin at column 1, right margin at the line length column, and tabs every 8 columns. The change option (#6) allows the user to interactively set the margins and tab stops by following the printed directions.

The typewriter settings available within SetUp mode are:

## 5. Operation

### 5.1 Powering On

When Cadetwriter is powered on, it performs a Power‐On Self‐Test (POST), restores all internal settings, flashes all of the indicator lights, resets the printwheel and ribbon, returns the carriage, beeps, moves over line offset spaces, and optionally sets all margins and tabs.

The POST reports firmware execution by turning on the orange LED when the startup code begins, turns off the orange LED when the startup code finishes and the main code begins, and blinks the blue LED for the first 5 seconds that keyboard scanning is occurring. After the POST, the orange and blue LEDs revert to indicating when an error or warning has occurred.

The margin / tab setting is done when the batteries installed setting is false or the hardware emulation jumpers have changed since the last power on. To set the margins and tabs, the carriage moves across the entire line and the printwheel spins as each margin and tab stop is set.

### 5.2 Using the Terminal

In general, Cadetwriter functions like any computer teleprinter. Here are the unique characteristics:
- Three keys (Code [Control], Esc, and | \) are in non‐standard locations.

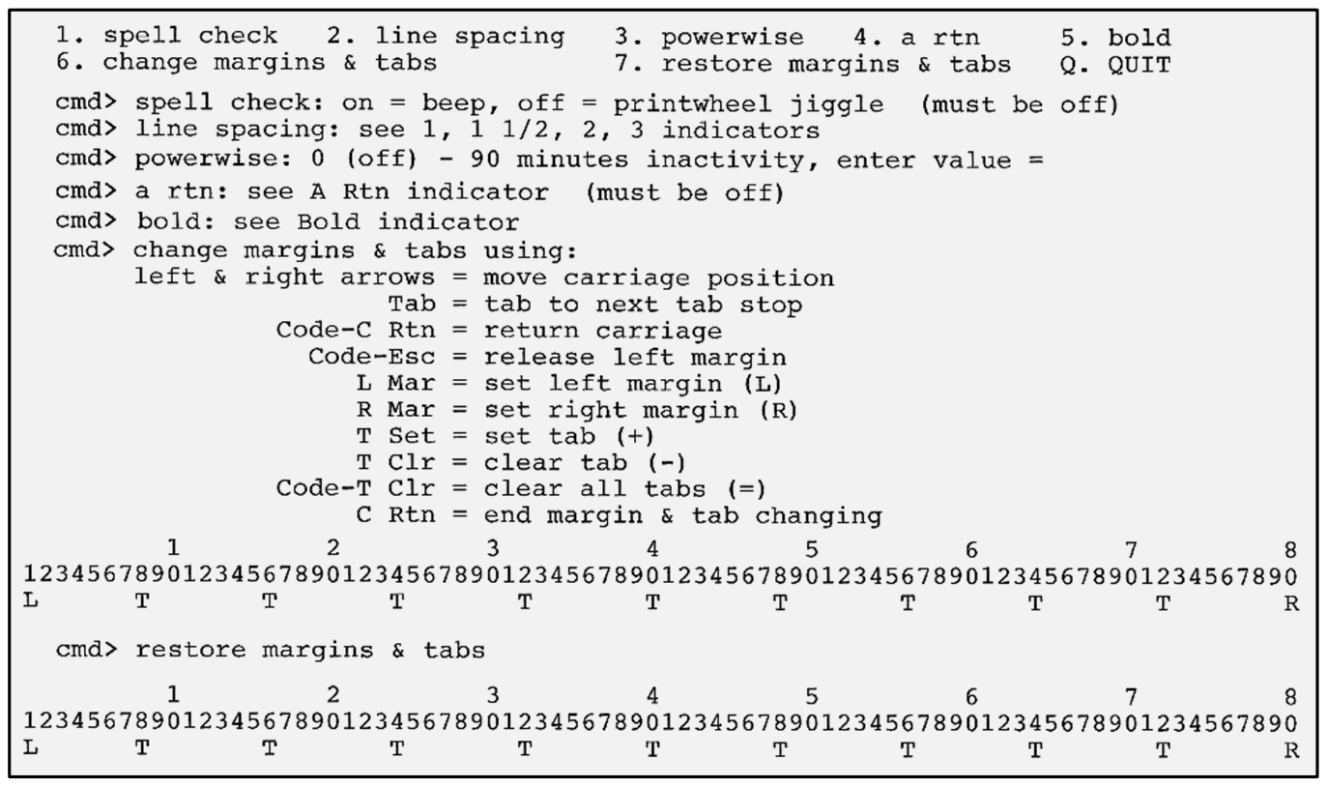
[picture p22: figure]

- The key labelled Code is the Ctrl (control) key.
- The arrow keys on the lower‐right of the keyboard cause local carriage movement – up, down, left, right. Ctrl‐<up arrow> and Ctrl‐<down arrow> cause the carriage to roll up and down micro positions. Ctrl‐CRtn performs a local carriage return. No data is sent to the computer for any of these local carriage movements.
- The movement keys – up arrow, left arrow, down arrow, right arrow, space, and backspace – are auto‐repeating. If they are depressed for more than six seconds, they repeat at a 10 cps rate until released.
- The L Mar, R Mar, T Set, and T Clr keys on the left side of the keyboard are used to set/clear margins and tabs. These function locally and no data is sent to the computer. First, position the carriage to the desired position using the arrow keys, then press the appropriate key to set/clear a margin or a tab. The typewriter will respond with a beep or jiggling the printwheel. Margin and tab locations are preserved in the EEPROM.

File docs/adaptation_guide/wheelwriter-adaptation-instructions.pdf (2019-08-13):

## Cadetwriter: IBM/Lexmark Wheelwriter 1000 Teleprinter Adaptation

https://github.com/IBM-1620/ (https://github.com/IBM-1620/Cadetwriter/raw/master/docs/adaptation_guide/wheelwriter-adaptation-instructions.pdf) Cadetwriter (https://github.com/IBM-1620/Cadetwriter/raw/master/docs/adaptation_guide/wheelwriter-adaptation-instructions.pdf) /raw/master/docs/ (https://github.com/IBM-1620/Cadetwriter/raw/master/docs/adaptation_guide/wheelwriter-adaptation-instructions.pdf) adaptation_guide/ (https://github.com/IBM-1620/Cadetwriter/raw/master/docs/adaptation_guide/wheelwriter-adaptation-instructions.pdf)wheelwriter-adaptation-instructions.pdf (https://github.com/IBM-1620/Cadetwriter/raw/master/docs/adaptation_guide/wheelwriter-adaptation-instructions.pdf)

The IBM 1620 Jr. project sponsored by the Computer History Museum is recreating the experience of running historic software on a 1960s-era computer by bringing a real IBM 1620 console to life with a cycle-accurate simulation running on a modern microcomputer. An integral part of the IBM 1620 console is the attached typewriter used to enter booting instructions and interact with programs. The typewriters used on the original machines were the IBM Model B and the IBM Selectric with nonstandard keyboard configurations, neither of which is practical to use for the recreation. Instead, a more recent IBM/Lexmark Wheelwriter 1000 typewriter has been adapted by interposing a microcontroller between the typewriter’s keyboard and logic board and installing custom keycaps. This allows keys pressed on the keyboard to be captured and interpreted according to the IBM 1620 layout and then sent to the simulator over a USB serial link. Conversely, the simulator can send characters that are then printed by injecting virtual keypresses to the logic board.

Some other historical computer projects have a similar need for a computer-interfaced typewriter or teletype and could use the same approach with the microcontroller firmware operating in ASCII mode. This document provides instructions for modifying an IBM/Lexmark Wheelwriter 1000 typewriter (Type 6781-024) to make a “Cadetwriter” as was done for the IBM 1620 Jr. project. These instructions may work with other model Wheelwriters, but that has not been verified. The tasks include building the USB & RS232 Interface Board Rev. 2.0 and RS232 cable; drilling and cutting holes in the typewriter case to mount the added interface board and the USB-B and RS232 cables; installing the interface board and cables connecting it to the logic board; and replacing the keycaps with the ASCII set. The following block diagram shows the adaptation.

## Cadetwriter: IBM/Lexmark Wheelwriter 1000 Teleprinter Adaptation

https://github.com/IBM-1620/ (https://github.com/IBM-1620/Cadetwriter/raw/master/docs/adaptation_guide/wheelwriter-adaptation-instructions.pdf) Cadetwriter (https://github.com/IBM-1620/Cadetwriter/raw/master/docs/adaptation_guide/wheelwriter-adaptation-instructions.pdf) /raw/master/docs/ (https://github.com/IBM-1620/Cadetwriter/raw/master/docs/adaptation_guide/wheelwriter-adaptation-instructions.pdf) adaptation_guide/ (https://github.com/IBM-1620/Cadetwriter/raw/master/docs/adaptation_guide/wheelwriter-adaptation-instructions.pdf)wheelwriter-adaptation-instructions.pdf (https://github.com/IBM-1620/Cadetwriter/raw/master/docs/adaptation_guide/wheelwriter-adaptation-instructions.pdf)

The IBM 1620 Jr. project sponsored by the Computer History Museum is recreating the experience of running historic software on a 1960s-era computer by bringing a real IBM 1620 console to life with a cycle-accurate simulation running on a modern microcomputer. An integral part of the IBM 1620 console is the attached typewriter used to enter booting instructions and interact with programs. The typewriters used on the original machines were the IBM Model B and the IBM Selectric with nonstandard keyboard configurations, neither of which is practical to use for the recreation. Instead, a more recent IBM/Lexmark Wheelwriter 1000 typewriter has been adapted by interposing a microcontroller between the typewriter’s keyboard and logic board and installing custom keycaps. This allows keys pressed on the keyboard to be captured and interpreted according to the IBM 1620 layout and then sent to the simulator over a USB serial link. Conversely, the simulator can send characters that are then printed by injecting virtual keypresses to the logic board.

Some other historical computer projects have a similar need for a computer-interfaced typewriter or teletype and could use the same approach with the microcontroller firmware operating in ASCII mode. This document provides instructions for modifying an IBM/Lexmark Wheelwriter 1000 typewriter (Type 6781-024) to make a “Cadetwriter” as was done for the IBM 1620 Jr. project. These instructions may work with other model Wheelwriters, but that has not been verified. The tasks include building the USB & RS232 Interface Board Rev. 2.0 and RS232 cable; drilling and cutting holes in the typewriter case to mount the added interface board and the USB-B and RS232 cables; installing the interface board and cables connecting it to the logic board; and replacing the keycaps with the ASCII set. The following block diagram shows the adaptation.

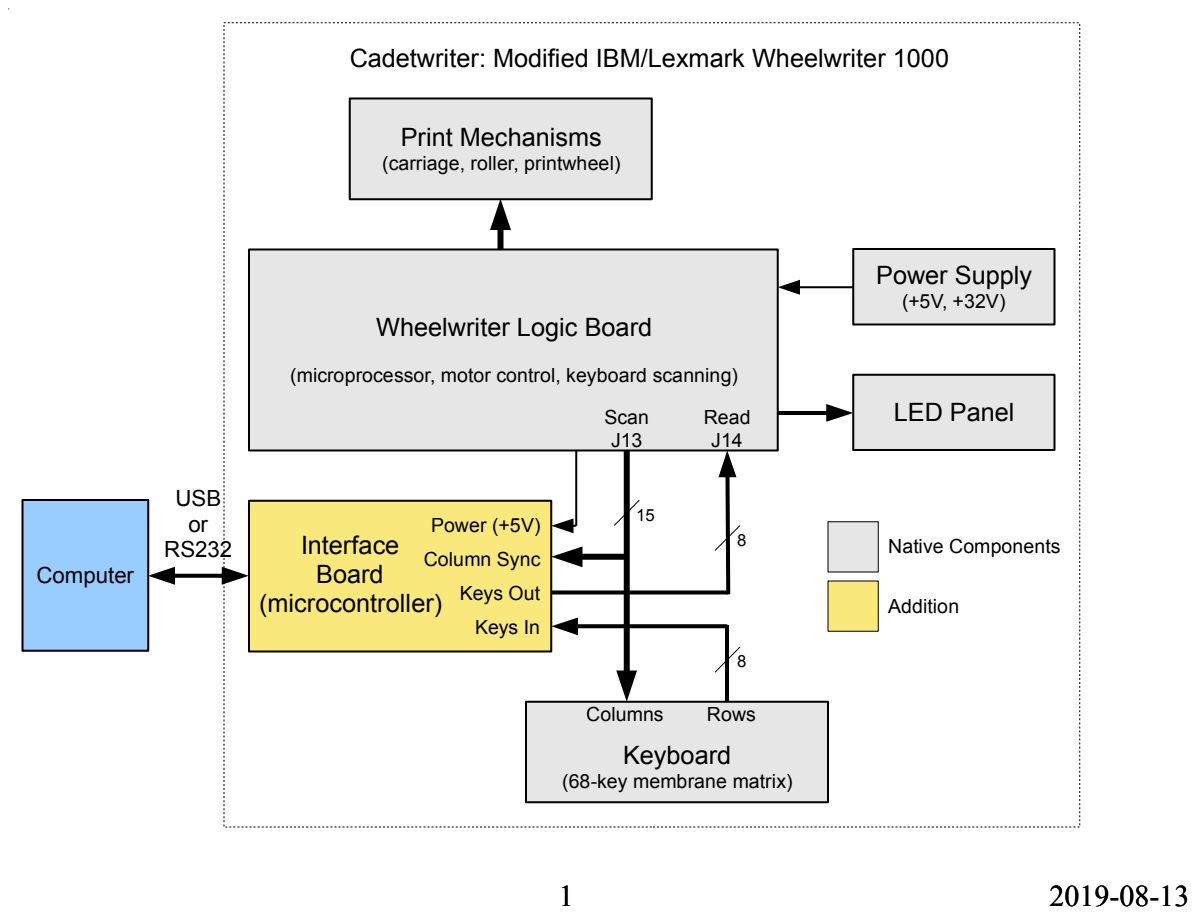
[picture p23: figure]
Wheelwriter Logic Board; (microprocessor, motor control, keyboard scanning); Print Mechanisms (carriage, roller, printwheel); LED Panel; Power Supply (+5V, +32V); Power (+5V); Column Sync; Keys Out; Keys In; Keyboard (68-key membrane matrix); Computer; Interface Board (microcontroller); Columns; Rows; USB or; Cadetwriter: Modified IBM/Lexmark Wheelwriter 1000; Native Components; Addition; Scan J13; Read J14

USB & RS232 Interface Board Rev. 2.0 Assembly
1. If no 6-520314-5 right-angle FFC connectors are available, two 6-520315-5 vertical FFC connectors can be modified for right-

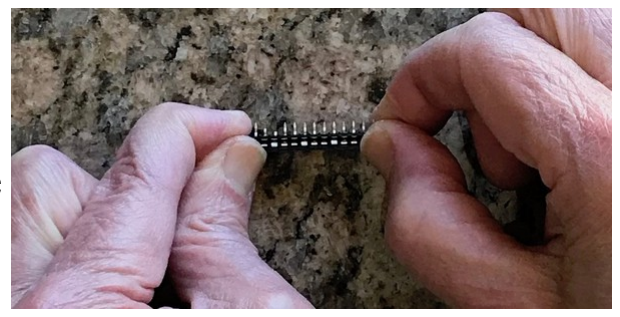
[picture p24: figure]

angle mounting instead. First use needle-nose pliers to flatten the alternating kinks in the pins, then use a hard surface to bend the pins 90° toward the ribbed side. Test easily dropping into place.
2. To hold the connectors in the right-angle orientation at J3 and J4,
deposit a thin bead of epoxy in the bare area along the edge closer
to the board edge, then set the connectors in place with the pins through the pads and let cure.
3. Insert two vertical 6-520315-5 FFC connectors in J1 and J2 in the orientation shown by the outline on the board, then solder all four FFC connectors.
4. Solder the 22-27-2021 2-pin connector in J5 with the latch side toward the edge of the board and the 2510-6002 10-pin connector in J10 with the notch side toward the edge of the board.
5. Insert and solder resistors, capacitors, blue LED1, green LED2 RxD, and red LED3 TxD.
6. Insert the three DIPs (74LS540 and MAX3232E ICs and the resistor array) using a pin-squeezing tool or by first bending the pins straight against a hard surface, then solder them.
7. Insert and solder the transistor (after the ICs so it's not in the way of the insertion tool).
8. Insert and solder the three 2-pin headers J6, J7 and J8 and install jumpers on J7 and J8 to configure for ASCII terminal mode and enable the RxD and TxD LEDs.
9. Cut the VIN - VUSB trace on the underside of the Teensy board.

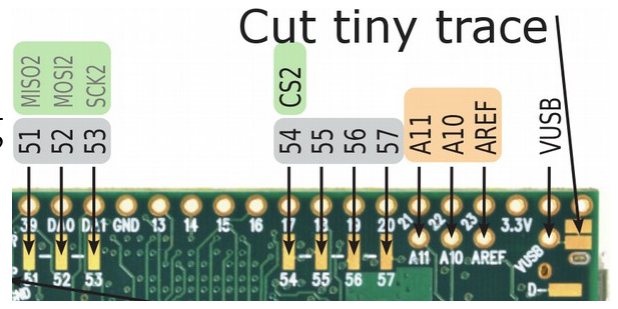
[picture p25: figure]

10. If using SIL header pins with the Teensy, cut them to 24 pins long
and insert them into the 48-pin socket, then set the Teensy board
over the pins to solder, noting pin 1. If using a Teensy with
preinstalled pins, attach the 24x1 sockets onto the Teensy pins.
11. Insert the Teensy socket with the Teensy in place, noting the right orientation, and solder.
12. Clip all component leads on the back side of the board to avoid damaging FFC cables.
13. (optional) Clean with solvent to remove flux.

USB & RS232 Interface Board Rev. 2.0 Assembly
1. If no 6-520314-5 right-angle FFC connectors are available, two 6-520315-5 vertical FFC connectors can be modified for right-angle mounting instead. First use needle-nose pliers to flatten the alternating kinks in the pins, then use a hard surface to bend the pins 90° toward the ribbed side. Test easily dropping into place.
2. To hold the connectors in the right-angle orientation at J3 and J4,
deposit a thin bead of epoxy in the bare area along the edge closer
to the board edge, then set the connectors in place with the pins through the pads and let cure.
3. Insert two vertical 6-520315-5 FFC connectors in J1 and J2 in the orientation shown by the outline on the board, then solder all four FFC connectors.
4. Solder the 22-27-2021 2-pin connector in J5 with the latch side toward the edge of the board and the 2510-6002 10-pin connector in J10 with the notch side toward the edge of the board.
5. Insert and solder resistors, capacitors, blue LED1, green LED2 RxD, and red LED3 TxD.
6. Insert the three DIPs (74LS540 and MAX3232E ICs and the resistor array) using a pin-squeezing tool or by first bending the pins straight against a hard surface, then solder them.
7. Insert and solder the transistor (after the ICs so it's not in the way of the insertion tool).
8. Insert and solder the three 2-pin headers J6, J7 and J8 and install jumpers on J7 and J8 to configure for ASCII terminal mode and enable the RxD and TxD LEDs.
9. Cut the VIN - VUSB trace on the underside of the Teensy board.
10. If using SIL header pins with the Teensy, cut them to 24 pins long
and insert them into the 48-pin socket, then set the Teensy board
over the pins to solder, noting pin 1. If using a Teensy with
preinstalled pins, attach the 24x1 sockets onto the Teensy pins.
11. Insert the Teensy socket with the Teensy in place, noting the right orientation, and solder.
12. Clip all component leads on the back side of the board to avoid damaging FFC cables.
13. (optional) Clean with solvent to remove flux.

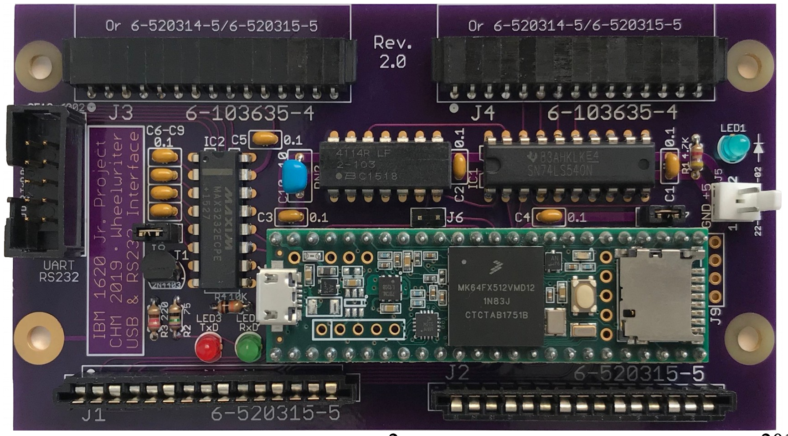
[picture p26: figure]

Build RS232 Cable
The following instructions tell how to build an RS232 serial cable using the ribbon cable and connectors in the parts list to go between the USB & RS232 Interface Board and a DE-9 connector mounted on the knockout panel at the back of the

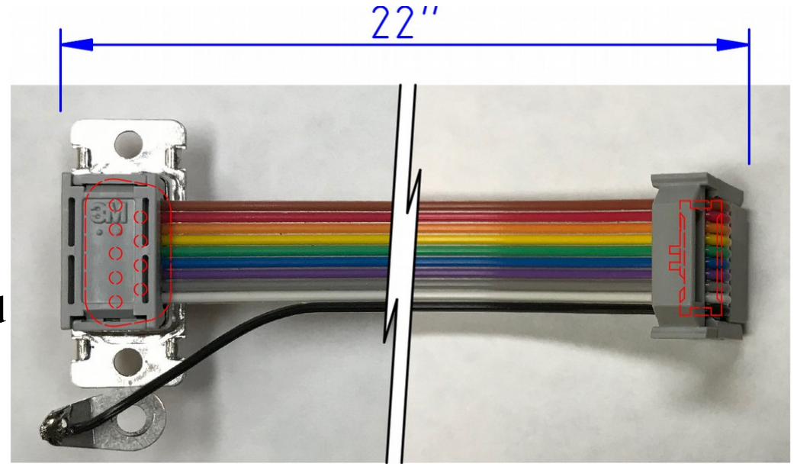
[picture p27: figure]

Wheelwriter. A male DE-9 connector was selected since it is standard for Data Terminal Equipment (DTE). If you want to use a female DE-9
connector in the standard Data Communications
Equipment (DCE) configuration with data
transmitted by the typewriter coming out of pin 2, then you will need to split the wires of the ribbon cable to swap the 3rd and 5th wires and the 4th and 6th wires. With a rainbow cable as shown in the photo, that would be brown, red, green, blue, orange, yellow, violet, gray, white. The cable included in the parts list has all gray wires with a red stripe for pin 1 (which is the brown wire in the photo).
1. Select a 24” piece of ribbon cable. The wiring shown here uses a 10-wire ribbon cable where the 10th wire is connected to a solder lug for grounding the DE-9 shell. If the Wheelwriter is one that does not have an aluminum shield on the inside of the base, or if this grounding is not desired, a 9-wire ribbon cable can be used instead in which case the result would be as in the photo but with the black wire removed.
2. Place the ribbon cable onto the pins of the 2x5 IDC ribbon cable socket with about an inch extending on the side with the index bumps. The rest would be extending to the right with the socket oriented as in the photo. Snap the cover on over the cable and clamp in a vise or with water pump pliers while holding the cable square to the connector. After clamping use diagonal cutters to remove the extra inch of ribbon cable on the side with the index bumps. Fold the ribbon cable back over the top of the cover (so it heads left as in the photo) and snap on the strain relief.
3. Place the other end of the ribbon cable onto the pins of the DE-9 connector in the orientation shown in the photo with about 1” extending past the connector. Snap on the adhesive cover and clamp, then trim the excess.

Note 1: The RS232 DSR signal is looped back to DTR in a labelled trace on the bottom side of the USB & RS232 Interface Board. Cut the trace if that loopback is not desired.
Note 2: Some desktop PCs use a similarly wired cable to connect from a 10-pin IDC connector on the motherboard to a male DE-9 connector on the back panel, so it might be possible to use a pre-made cable. However, there are some considerations:
1. There are two industry standard pinout conventions in use, the AT/Everex and the DTK/Intel. This cable corresponds to the DTK/Intel convention; an AT/Everex cable would put the signals on the wrong pins. See http://www.bodenzord.com/archives/117 for an explanation of the differences.
2. Most cables available as standard products are only 12” long. That length would reach the back panel if routed directly, but then it would be under the carriage FFC cable that flexes back and forth as the carriage moves which might cause wear or interference.
3. These cables use a DE-9 connector intended for mounting behind a metal panel. The plastic knockout panel in the Wheelwriter case is too thick to leave enough depth for jackscrews on the outside of the panel if the connector is mounted behind the panel.

Build RS232 Cable
The following instructions tell how to build an RS232 serial cable using the ribbon cable and connectors in the parts list to go between the USB & RS232 Interface Board and a DE-9 connector mounted on the knockout panel at the back of the Wheelwriter. A male DE-9 connector was selected since it is standard for Data Terminal Equipment (DTE). If you want to use a female DE-9
connector in the standard Data Communications
Equipment (DCE) configuration with data
transmitted by the typewriter coming out of pin 2, then you will need to split the wires of the ribbon cable to swap the 3rd and 5th wires and the 4th and 6th wires. With a rainbow cable as shown in the photo, that would be brown, red, green, blue, orange, yellow, violet, gray, white. The cable included in the parts list has all gray wires with a red stripe for pin 1 (which is the brown wire in the photo).
1. Select a 24” piece of ribbon cable. The wiring shown here uses a 10-wire ribbon cable where the 10th wire is connected to a solder lug for grounding the DE-9 shell. If the Wheelwriter is one that does not have an aluminum shield on the inside of the base, or if this grounding is not desired, a 9-wire ribbon cable can be used instead in which case the result would be as in the photo but with the black wire removed.
2. Place the ribbon cable onto the pins of the 2x5 IDC ribbon cable socket with about an inch extending on the side with the index bumps. The rest would be extending to the right with the socket oriented as in the photo. Snap the cover on over the cable and clamp in a vise or with water pump pliers while holding the cable square to the connector. After clamping use diagonal cutters to remove the extra inch of ribbon cable on the side with the index bumps. Fold the ribbon cable back over the top of the cover (so it heads left as in the photo) and snap on the strain relief.
3. Place the other end of the ribbon cable onto the pins of the DE-9 connector in the orientation shown in the photo with about 1” extending past the connector. Snap on the adhesive cover and clamp, then trim the excess.

Note 1: The RS232 DSR signal is looped back to DTR in a labelled trace on the bottom side of the USB & RS232 Interface Board. Cut the trace if that loopback is not desired.
Note 2: Some desktop PCs use a similarly wired cable to connect from a 10-pin IDC connector on the motherboard to a male DE-9 connector on the back panel, so it might be possible to use a pre-made cable. However, there are some considerations:
1. There are two industry standard pinout conventions in use, the AT/Everex and the DTK/Intel. This cable corresponds to the DTK/Intel convention; an AT/Everex cable would put the signals on the wrong pins. See http://www.bodenzord.com/archives/117 for an explanation of the differences.
2. Most cables available as standard products are only 12” long. That length would reach the back panel if routed directly, but then it would be under the carriage FFC cable that flexes back and forth as the carriage moves which might cause wear or interference.
3. These cables use a DE-9 connector intended for mounting behind a metal panel. The plastic knockout panel in the Wheelwriter case is too thick to leave enough depth for jackscrews on the outside of the panel if the connector is mounted behind the panel.

Wheelwriter Case Modifications
1. Pull the paper release and paper bail load levers forward.
2. Remove the top half of the Wheelwriter case by inserting a thin screwdriver into the top of the slots in the lower half of the case

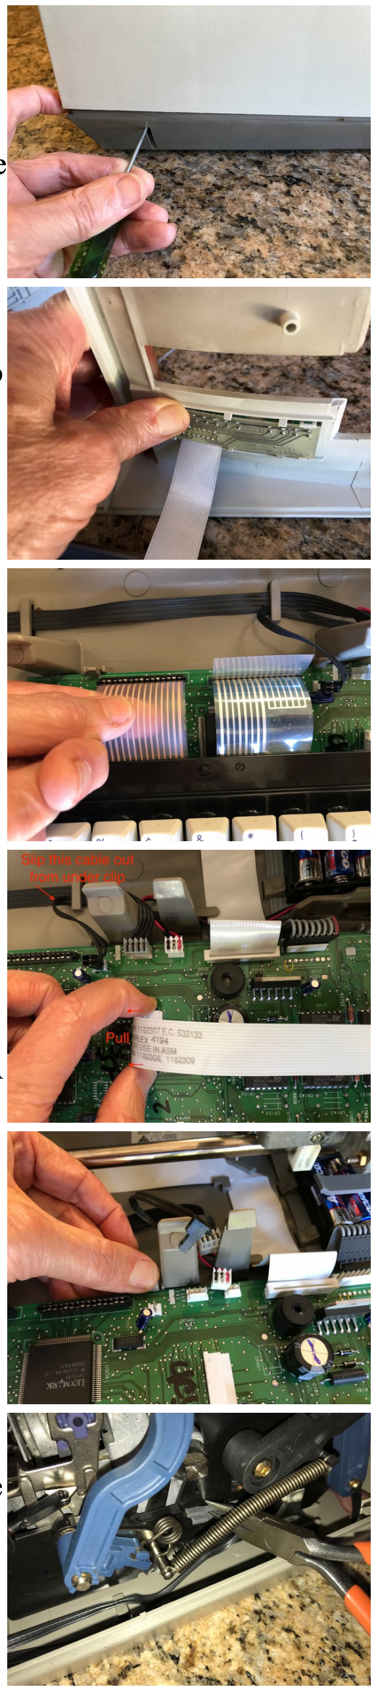
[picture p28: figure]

on each side near the back and pushing in on the latches to release the top half, then rotate the top half upwards from the rear while sliding towards the front. The top will still be tethered by a cable to the LED display panel.

3. Gently push on the back side of the LED panel to disengage it from the top half of the case, then feed it back through the hole so the top half is completely free.
4. Remove the ribbon cartridge by pushing on the release lever and then lifting up and out, then manually push the carriage all the way to the right so it is out of the way.
5. Remove the keyboard from its

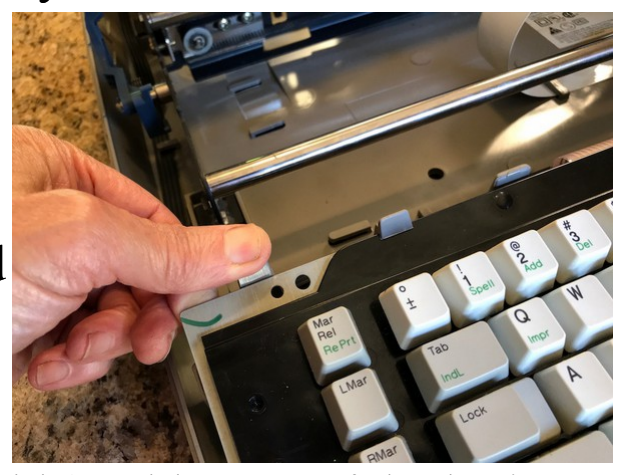
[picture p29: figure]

mounting by releasing four latches
along the back edge of the
keyboard and then rotating upward slightly and pulling the keyboard
out from the catches at the front.
Then you can set the keyboard
down and pull the FFC (flat flex cable) cables out of the logic board connectors.
6. Unplug all the cables connected to the logic board. The connectors for the two white FFC cables are zero-insertion-force connectors where you pull on the clamp tabs to release the cable. All the other connectors lift straight up, but the 8-wire cable J15A is quite stiff and requires some force to lift. The black two-wire cable going to J3 needs to be slipped out from under the clip in the base and rerouted since the USB & RS232 Interface Board will cover that clip.
7. Remove the logic board by releasing three latches along the back edge and lifting it out of the catches at the front.
8. Unplug the connectors from the two servo motors at the back of the case (for platen rotation and carriage motion).
9. Unplug the two wires from tabs on the switch at the bottom of the paper bail load lever. It is not necessary to keep track of which wire was connected to which tab.

Wheelwriter Case Modifications
1. Pull the paper release and paper bail load levers forward.
2. Remove the top half of the Wheelwriter case by inserting a thin screwdriver into the top of the slots in the lower half of the case on each side near the back and pushing in on the latches to release the top half, then rotate the top half upwards from the rear while sliding towards the front. The top will still be tethered by a cable to the LED display panel.
3. Gently push on the back side of the LED panel to disengage it from the top half of the case, then feed it back through the hole so the top half is completely free.
4. Remove the ribbon cartridge by pushing on the release lever and then lifting up and out, then manually push the carriage all the way to the right so it is out of the way.
5. Remove the keyboard from its
mounting by releasing four latches
along the back edge of the
keyboard and then rotating upward slightly and pulling the keyboard
out from the catches at the front.
Then you can set the keyboard
down and pull the FFC (flat flex cable) cables out of the logic board connectors.
6. Unplug all the cables connected to the logic board. The connectors for the two white FFC cables are zero-insertion-force connectors where you pull on the clamp tabs to release the cable. All the other connectors lift straight up, but the 8-wire cable J15A is quite stiff and requires some force to lift. The black two-wire cable going to J3 needs to be slipped out from under the clip in the base and rerouted since the USB & RS232 Interface Board will cover that clip.
7. Remove the logic board by releasing three latches along the back edge and lifting it out of the catches at the front.
8. Unplug the connectors from the two servo motors at the back of the case (for platen rotation and carriage motion).
9. Unplug the two wires from tabs on the switch at the bottom of the paper bail load lever. It is not necessary to keep track of which wire was connected to which tab.

10. Push the carriage back to the left and slip the carriage FFC cable out from under the clip in the center of the case bottom. Insert a round object such as a center punch or pencil between the two layers of the carriage FFC cable where it makes a 90° bend in order to slip the cable out from under the inner clip at that corner, then slide the cable out from under the outer clip.
11. Remove the whole frame assembly by releasing the four clips at the corners of the frame assembly. Use a twisting motion with a large screwdriver on the inside of the sheet metal frame members

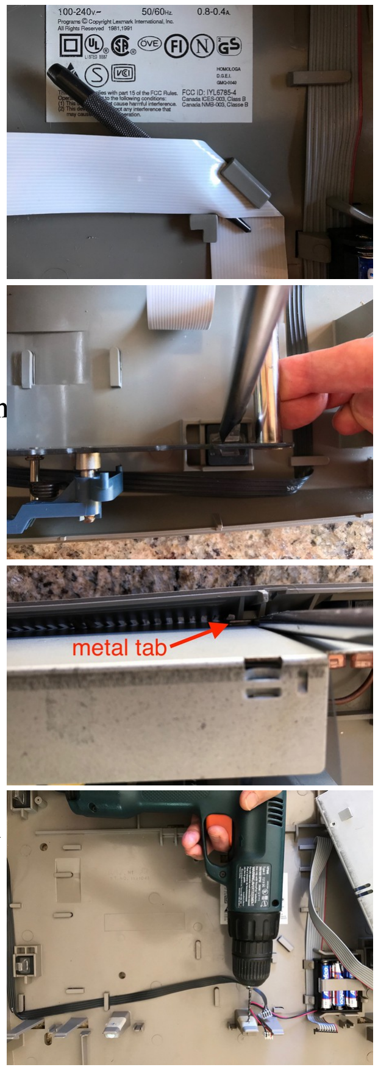
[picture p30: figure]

(except the right rear which is outside) to pry the latches free from the slots in the frame while lifting the frame to completely
remove it. The latch has to bend back more than 1/8” before it is free of the frame.
12. Move the power supply out of the way by prying two catches in the back side of the plastic base away from tabs on back side of the power supply’s metal case and rotating the power supply out of the way (no need to unplug the AC connectors).
13. Drill 3/32" holes in the two keyboard support posts adjacent on both sides of where the USB & RS232 Interface Board will go, located 1.35" from the floor of the Wheelwriter case and centered in the width of each post. Marking the location on a piece of masking tape and center-punching with an awl may help. Drill only through the near surface of the post which is less than 1/8” thick. Cut threads in both holes with a #4 truss head screw for
easier insertion later. Snap the power supply back into place and
slip its cable back under the clips in the base.
14. Slip the platen motor cable that runs along the left side of the base out from under its clips where it crosses the location where the USB & RS232 Interface Board will go in the middle of the base, and fold it back out of the way.
15. Print and cut out the two templates provided on a later page of this document. Verify that the printer scaling is accurate by measuring the dimensions as shown on the Wheelwriter USB & RS232 Interface Template, and reprint with adjusted scaling if necessary.

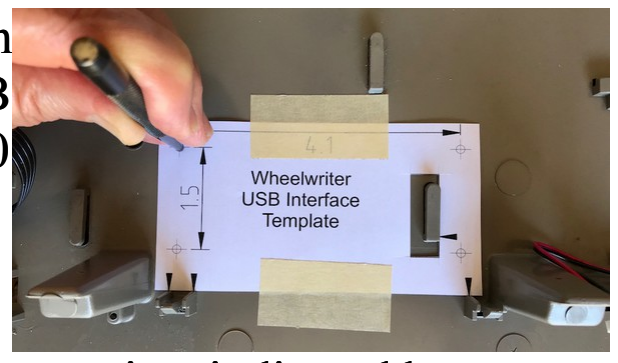
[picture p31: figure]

16. Place a scrap piece of 3/16” plywood or other material underneath
the middle of the base to support it where holes to mount the USB
& RS232 Interface Board will be drilled. For a Wheelwriter 1000
that has a thin aluminum static shield covering the base (not
present on the unit in these photographs), use masking tape along
edges of cutouts to hold the shield from moving. Position the
Wheelwriter USB & RS232 Interface Template against the reference points indicated by arrows, and tape in place. Center-punch for the four USB & RS232 Interface Board mounting holes indicated on the template. Drill 1/8" mounting holes from the top.
10. Push the carriage back to the left and slip the carriage FFC cable out from under the clip in the center of the case bottom. Insert a round object such as a center punch or pencil between the two layers of the carriage FFC cable where it makes a 90° bend in order to slip the cable out from under the inner clip at that corner, then slide the cable out from under the outer clip.
11. Remove the whole frame assembly by releasing the four clips at the corners of the frame assembly. Use a twisting motion with a large screwdriver on the inside of the sheet metal frame members (except the right rear which is outside) to pry the latches free from the slots in the frame while lifting the frame to completely
remove it. The latch has to bend back more than 1/8” before it is free of the frame.
12. Move the power supply out of the way by prying two catches in the back side of the plastic base away from tabs on back side of the power supply’s metal case and rotating the power supply out of the way (no need to unplug the AC connectors).
13. Drill 3/32" holes in the two keyboard support posts adjacent on both sides of where the USB & RS232 Interface Board will go, located 1.35" from the floor of the Wheelwriter case and centered in the width of each post. Marking the location on a piece of masking tape and center-punching with an awl may help. Drill only through the near surface of the post which is less than 1/8” thick. Cut threads in both holes with a #4 truss head screw for
easier insertion later. Snap the power supply back into place and
slip its cable back under the clips in the base.
14. Slip the platen motor cable that runs along the left side of the base out from under its clips where it crosses the location where the USB & RS232 Interface Board will go in the middle of the base, and fold it back out of the way.
15. Print and cut out the two templates provided on a later page of this document. Verify that the printer scaling is accurate by measuring the dimensions as shown on the Wheelwriter USB & RS232 Interface Template, and reprint with adjusted scaling if necessary.
16. Place a scrap piece of 3/16” plywood or other material underneath
the middle of the base to support it where holes to mount the USB
& RS232 Interface Board will be drilled. For a Wheelwriter 1000
that has a thin aluminum static shield covering the base (not
present on the unit in these photographs), use masking tape along
edges of cutouts to hold the shield from moving. Position the
Wheelwriter USB & RS232 Interface Template against the reference points indicated by arrows, and tape in place. Center-punch for the four USB & RS232 Interface Board mounting holes indicated on the template. Drill 1/8" mounting holes from the top.

17. From the underside of the case, countersink the four mounting holes for the USB & RS232 Interface Board standoffs so the flat-head screws will be below the surface.

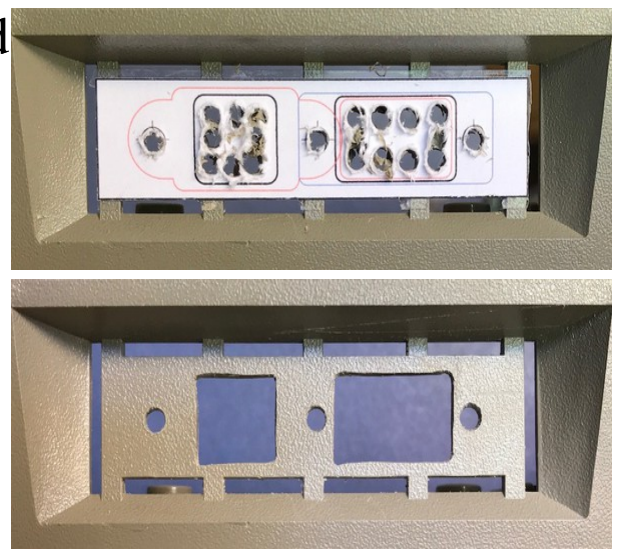
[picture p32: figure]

18. The second template shows the cutout patterns for the USB-B and
DE-9 RS232 connectors. Two variants are provided; the one
pictured shares one screw between the two connectors. Use
double-sided tape to attach it to the knockout panel in the rear of the lower half of the case (on the right as viewed from the rear). Use an awl to center-punch for the mounting screw holes and holes at the corners and midpoints of the center cutout areas, then drill 1/8" holes for the mounting screws, corners and midpoints. Clear out the cutouts to the black lines with snips, saw, file, razor knife and/or Dremel tool.

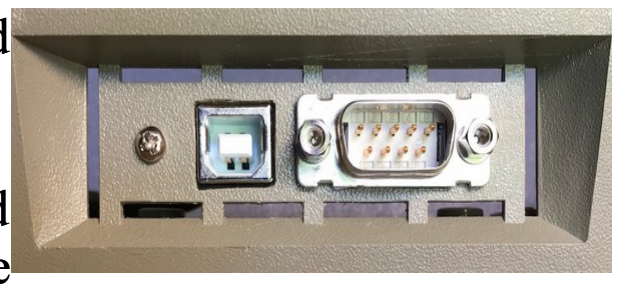
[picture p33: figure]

19. Use a file or razor knife to shave about 1/32” of the plastic around the captive nut on the right side of the USB-B panel-mount connector to ease the fit next to the back side of the DE-9
connector. Install the USB-B connector using one of the provided
screws on the left. Thread the 2x5 IDC socket of the RS232 cable
through the cutout and install the DE-9 connector on the outside of the panel using two jackscrews with one flat washer on the outside. The middle jackscrew threads into the USB-B connector. The jackscrew on the right gets the solder lug (if used), then a flat washer, lock washer and nut.
20. Route the ribbon cable underneath the USB cable as pictured,

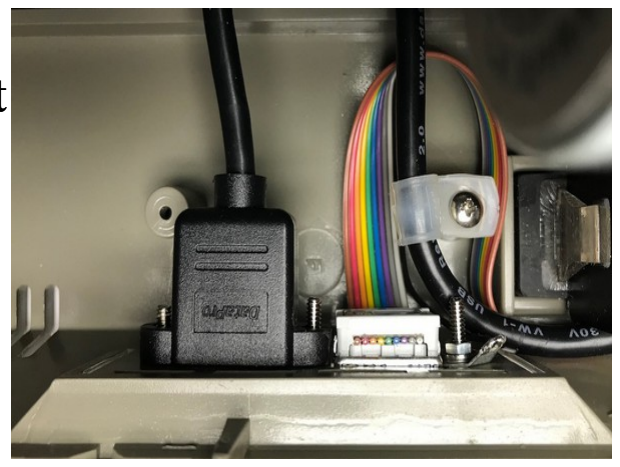
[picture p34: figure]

then restrain the USB cable with a cable clamp screwed to the left
post inside the knockout panel area using one of the #4 truss head sheet metal screws.
21. Set the frame assembly loosely back in position making sure not
to pinch any cables.
22. Connect the two wires to the tabs on the switch at the bottom of the paper bail load lever. It does not matter which wire goes to which tab.
23. Slide the carriage FFC cable back into the corner clips so the bottom layer is under the inner corner clip and then the fold slides into the outer corner clip. Then insert the round object to bow up the upper layer to get it under the inner corner clip. Also slide the cable back under the clip in the center of its track.
24. Push the frame assembly back down into its four corner latches.
25. Plug in the ribbon cables for the two servo motors at the back.
26. Slip the platen motor cable back under its clips where it will cross under the USB & RS232 Interface Board.
17. From the underside of the case, countersink the four mounting holes for the USB & RS232 Interface Board standoffs so the flat-head screws will be below the surface.
18. The second template shows the cutout patterns for the USB-B and
DE-9 RS232 connectors. Two variants are provided; the one
pictured shares one screw between the two connectors. Use
double-sided tape to attach it to the knockout panel in the rear of the lower half of the case (on the right as viewed from the rear). Use an awl to center-punch for the mounting screw holes and holes at the corners and midpoints of the center cutout areas, then drill 1/8" holes for the mounting screws, corners and midpoints. Clear out the cutouts to the black lines with snips, saw, file, razor knife and/or Dremel tool.
19. Use a file or razor knife to shave about 1/32” of the plastic around the captive nut on the right side of the USB-B panel-mount connector to ease the fit next to the back side of the DE-9
connector. Install the USB-B connector using one of the provided
screws on the left. Thread the 2x5 IDC socket of the RS232 cable
through the cutout and install the DE-9 connector on the outside of the panel using two jackscrews with one flat washer on the outside. The middle jackscrew threads into the USB-B connector. The jackscrew on the right gets the solder lug (if used), then a flat washer, lock washer and nut.
20. Route the ribbon cable underneath the USB cable as pictured,
then restrain the USB cable with a cable clamp screwed to the left
post inside the knockout panel area using one of the #4 truss head sheet metal screws.
21. Set the frame assembly loosely back in position making sure not
to pinch any cables.
22. Connect the two wires to the tabs on the switch at the bottom of the paper bail load lever. It does not matter which wire goes to which tab.
23. Slide the carriage FFC cable back into the corner clips so the bottom layer is under the inner corner clip and then the fold slides into the outer corner clip. Then insert the round object to bow up the upper layer to get it under the inner corner clip. Also slide the cable back under the clip in the center of its track.
24. Push the frame assembly back down into its four corner latches.
25. Plug in the ribbon cables for the two servo motors at the back.
26. Slip the platen motor cable back under its clips where it will cross under the USB & RS232 Interface Board.

Logic Board Modifications
1. Use a desoldering tool or solder wick to remove solder from the leftmost 3 holes of unpopulated J9 on the logic board (in the right rear corner).
2. Install a 22-27-2031 3-pin Molex connector in the leftmost 3
holes of J9 with the latch away from the edge of the board.
3. (optional) Clean soldered areas with solvent to remove flux.

Install ASCII Keycaps

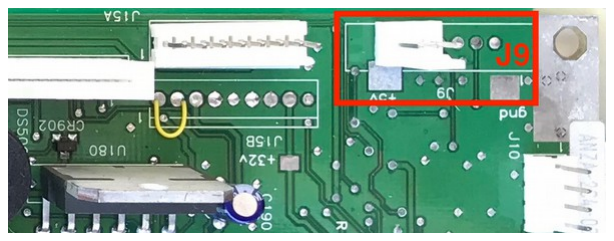
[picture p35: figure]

The original keycaps of the Wheelwriter keyboard do not show all the ASCII characters, but they can be replaced with new keycaps from Unicomp, Inc. who still make modern keyboards using the same underlying key mechanism.
The appropriate keycap placement is shown in the following photo. The old keycaps can be removed simply by prying them up with a screwdriver. The new ones snap in place, being careful to position the spring into the stem of the new keycap.

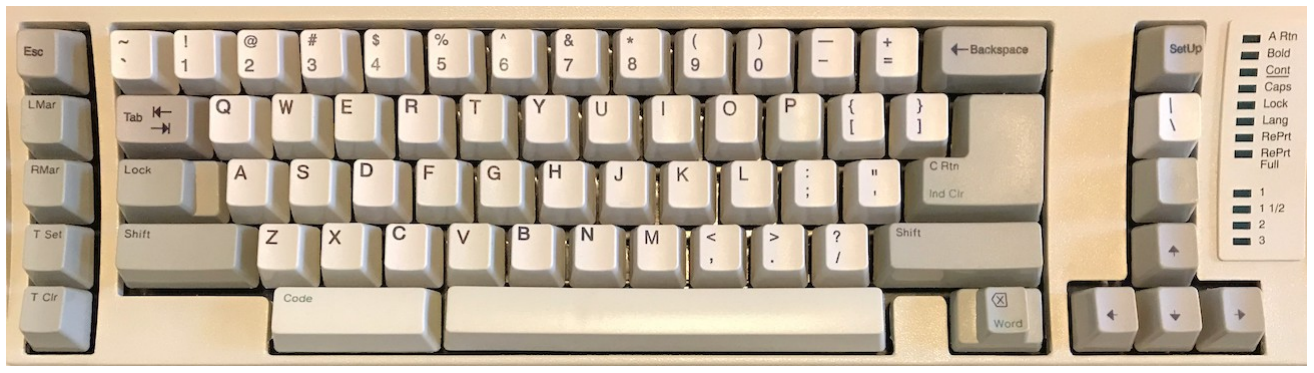
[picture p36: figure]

Install the USB & RS232 Interface Board and Cables
1. Attach four standoffs for mounting the USB & RS232 Interface Board using flat-head screws from the underside, but don't tighten them.
2. Reinstall the logic board but do not attach any cables yet.
3. Insert FFC interconnect cables into the Interface Board with the contacts facing up. The cable in J3 on the left has contacts on the
same side at both ends; the one in J4 on the right has opposite

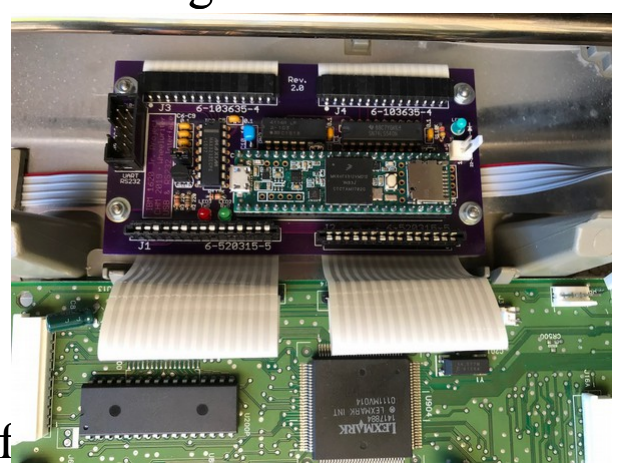
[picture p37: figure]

contacts. Fold the cables back under the board right at the edge of
the board. Plug the other end of the FFC interconnect cables into the logic board.
4. Install the Interface Board onto standoffs with washers and nuts. Finish tightening using a wrench or nutdriver on the nuts and tighten the screws from underneath.
5. Where the FFC interconnect cables come up from under the Interface Board by the logic board, pull the cables taut and fold them away from the Interface Board right at the connectors on the logic board, then crease the excess so they will stay under the keyboard (see photo above).

Logic Board Modifications
1. Use a desoldering tool or solder wick to remove solder from the leftmost 3 holes of unpopulated J9 on the logic board (in the right rear corner).
2. Install a 22-27-2031 3-pin Molex connector in the leftmost 3
holes of J9 with the latch away from the edge of the board.
3. (optional) Clean soldered areas with solvent to remove flux.

Install ASCII Keycaps
The original keycaps of the Wheelwriter keyboard do not show all the ASCII characters, but they can be replaced with new keycaps from Unicomp, Inc. who still make modern keyboards using the same underlying key mechanism.
The appropriate keycap placement is shown in the following photo. The old keycaps can be removed simply by prying them up with a screwdriver. The new ones snap in place, being careful to position the spring into the stem of the new keycap.

Install the USB & RS232 Interface Board and Cables
1. Attach four standoffs for mounting the USB & RS232 Interface Board using flat-head screws from the underside, but don't tighten them.
2. Reinstall the logic board but do not attach any cables yet.
3. Insert FFC interconnect cables into the Interface Board with the contacts facing up. The cable in J3 on the left has contacts on the
same side at both ends; the one in J4 on the right has opposite
contacts. Fold the cables back under the board right at the edge of
the board. Plug the other end of the FFC interconnect cables into the logic board.
4. Install the Interface Board onto standoffs with washers and nuts. Finish tightening using a wrench or nutdriver on the nuts and tighten the screws from underneath.
5. Where the FFC interconnect cables come up from under the Interface Board by the logic board, pull the cables taut and fold them away from the Interface Board right at the connectors on the logic board, then crease the excess so they will stay under the keyboard (see photo above).

6. Cut two 8” pieces of hookup wire, preferably red and black. Strip the ends about 1/8” and crimp on the Molex 08-50-0114 female pins. Twist the two wires together to make a cable. Insert the pins into the Molex 22-01-3027 2-pin housing so that red mates to the pin marked +5 on the Interface Board. At the other end, insert the pins into the Molex 22-01-3027 3-pin housing with black toward the corner of the logic board and red at the opposite end. The middle position is empty.
7. Install the new power cable from the logic board to the USB &
RS232 Interface Board, routing it underneath all the other cables
along the back edge of the logic board. Bend the wires down sharply at the connector on the USB & RS232 Interface Board to avoid interference with the carriage. Now reconnect all the
existing cables to the logic board. To insert the FFC cables for
the carriage and the LED panel, first pull the connector clamp

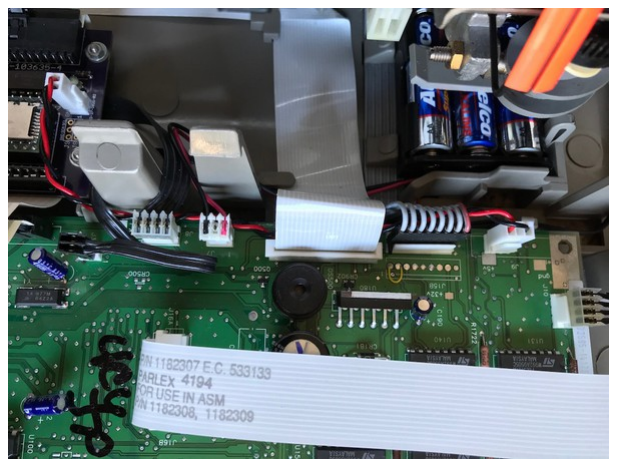
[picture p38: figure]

open, then insert the cable, then push the clamp closed. The black 2-wire ribbon cable to J3 on the logic board has excess length now because it no longer hooks through the clip that is now under the Interface Board, so bend that excess over the logic board.

8. Lay the keyboard loosely over its position and insert the FFC
cables from the keyboard into the connectors on the Interface
Board (this is not easy – it may require padded forceps). There will still be about 0.1” of the wide portion of the conductors above the top of the connectors when the cable is fully inserted.
9. Make a bracket to depress the keyboard FFC cables by manually

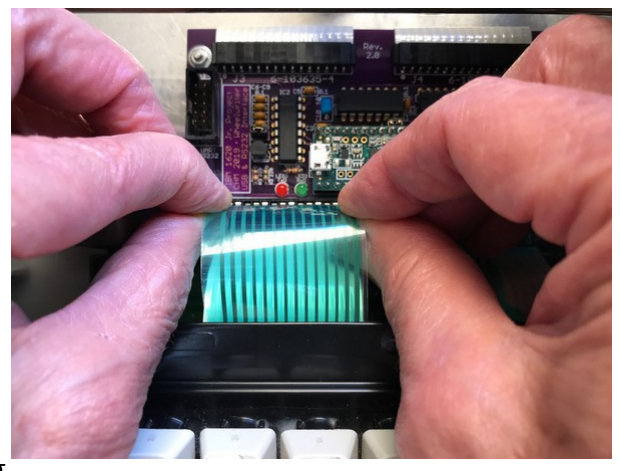
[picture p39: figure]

bending steel coat-hanger wire using needle-nose pliers according to the dimensions shown in the CAD diagram below.

10. Install the bracket to hold back the keyboard FFC cables using two #4 truss head screws into the holes drilled into the keyboard support posts.
11. Install the keyboard into its front catches and then rear clips.

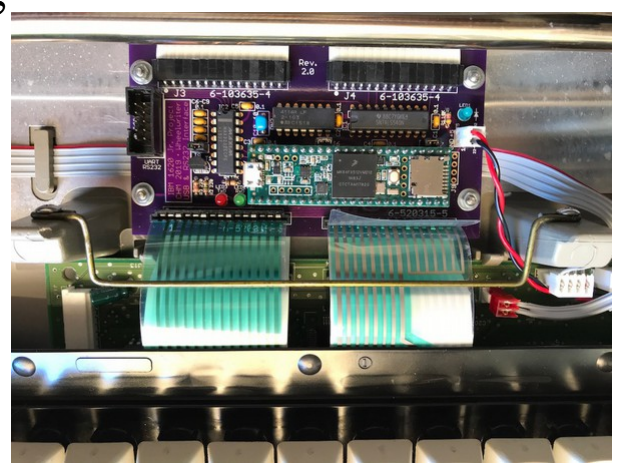
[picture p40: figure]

12. Plug the micro-USB connector into the Teensy and plug the RS232 ribbon cable into the board. Then adjust the position of the cables behind the left rear foot and restraining both cables with one or two cable ties to the existing clip for the platen motor ribbon cable at its front corner.
13. Plug in and power on the Wheelwriter. Plug a USB-B cable into the new panel connector at the back of the Wheelwriter and connect it to the host computer, then download appropriate firmware into the Teensy. It will be necessary to cycle power on the Wheelwriter after the download before the logic board will be properly operating with the firmware on the USB & RS232 Interface Board. Verify operation with appropriate test programs.
14. Reinstall the top half of the Wheelwriter case: pull the paper release and paper bale levers forward; thread the LED panel loosely through its hole in the case top; hook in the catches at the front of the machine and then tilt down the back until the latches meet and catch; and finally snap the LED panel back into place. The column index marker can be adjusted to line up with column 0. The “Artisan 10” printwheel #1353520 is recommended.
6. Cut two 8” pieces of hookup wire, preferably red and black. Strip the ends about 1/8” and crimp on the Molex 08-50-0114 female pins. Twist the two wires together to make a cable. Insert the pins into the Molex 22-01-3027 2-pin housing so that red mates to the pin marked +5 on the Interface Board. At the other end, insert the pins into the Molex 22-01-3027 3-pin housing with black toward the corner of the logic board and red at the opposite end. The middle position is empty.
7. Install the new power cable from the logic board to the USB &
RS232 Interface Board, routing it underneath all the other cables
along the back edge of the logic board. Bend the wires down sharply at the connector on the USB & RS232 Interface Board to avoid interference with the carriage. Now reconnect all the
existing cables to the logic board. To insert the FFC cables for
the carriage and the LED panel, first pull the connector clamp
open, then insert the cable, then push the clamp closed. The black 2-wire ribbon cable to J3 on the logic board has excess length now because it no longer hooks through the clip that is now under the Interface Board, so bend that excess over the logic board.
8. Lay the keyboard loosely over its position and insert the FFC
cables from the keyboard into the connectors on the Interface
Board (this is not easy – it may require padded forceps). There will still be about 0.1” of the wide portion of the conductors above the top of the connectors when the cable is fully inserted.
9. Make a bracket to depress the keyboard FFC cables by manually bending steel coat-hanger wire using needle-nose pliers according to the dimensions shown in the CAD diagram below.
10. Install the bracket to hold back the keyboard FFC cables using two #4 truss head screws into the holes drilled into the keyboard support posts.
11. Install the keyboard into its front catches and then rear clips.
12. Plug the micro-USB connector into the Teensy and plug the RS232 ribbon cable into the board. Then adjust the position of the cables behind the left rear foot and restraining both cables with one or two cable ties to the existing clip for the platen motor ribbon cable at its front corner.
13. Plug in and power on the Wheelwriter. Plug a USB-B cable into the new panel connector at the back of the Wheelwriter and connect it to the host computer, then download appropriate firmware into the Teensy. It will be necessary to cycle power on the Wheelwriter after the download before the logic board will be properly operating with the firmware on the USB & RS232 Interface Board. Verify operation with appropriate test programs.
14. Reinstall the top half of the Wheelwriter case: pull the paper release and paper bale levers forward; thread the LED panel loosely through its hole in the case top; hook in the catches at the front of the machine and then tilt down the back until the latches meet and catch; and finally snap the LED panel back into place. The column index marker can be adjusted to line up with column 0. The “Artisan 10” printwheel #1353520 is recommended.

Parts List
Count Count | RS232 Description RS232 Description | | Source Source | Source PN Source PN | Cost Note Cost Note
1 1 | | USB & RS232 Interface PCB USB & RS232 Interface PCB | OSH Park OSH Park | TIkAO4NE TIkAO4NE | 17.42 17.42 | 1 1
1 1 | | Teensy 3.5 without pins Teensy 3.5 without pins | PJRC PJRC | TEENSY35 TEENSY35 | 24.25 24.25 | 2 2
2 2 | | 32 SIL header pins for Teensy 32 SIL header pins for Teensy | DigiKey DigiKey | 952-2521-ND 952-2521-ND | 10.46 10.46 | 2 2
1 1 | | 48-pin socket for Teensy 48-pin socket for Teensy | DigiKey DigiKey | ED3648-ND ED3648-ND | 3.84 3.84 | 2 2
1 1 | | 74LS540 PDIP IC 74LS540 PDIP IC | DigiKey DigiKey | 296-3715-5-ND 296-3715-5-ND | 1.64 1.64
1 1 | 1 RS232 transceiver PDIP IC 1 RS232 transceiver PDIP IC | | DigiKey DigiKey | MAX3232ECPE+-ND MAX3232ECPE+-ND | 5.37 5.37 | 3 3
1 1 | 1 Transistor PNP 40V 0.6A TO-92 1 Transistor PNP 40V 0.6A TO-92 | | DigiKey DigiKey | 2N4403-ND 2N4403-ND | 0.30 0.30
1 1 | | 10K x 13 resistor network 10K x 13 resistor network | DigiKey DigiKey | 4114R-2-103LF-ND 4114R-2-103LF-ND | 1.12 1.12
9 9 | 4 0.1 µF capacitor 4 0.1 µF capacitor | | DigiKey DigiKey | 399-4264-ND 399-4264-ND | 1.50 1.50 | 4 4
1 1 | | 10 µF capacitor 10 µF capacitor | DigiKey DigiKey | 490-14508-ND 490-14508-ND | 1.21 1.21
1 1 | | 3mm LED (blue) for LED1 3mm LED (blue) for LED1 | DigiKey DigiKey | VAOL-3LSBY1-ND VAOL-3LSBY1-ND | 0.65 0.65 | 5 5
1 1 | 1 3mm LED (green) for LED2 RxD 1 3mm LED (green) for LED2 RxD | | DigiKey DigiKey | VAOL-3LDE2-ND VAOL-3LDE2-ND | 0.44 0.44 | 5 5
1 1 | 1 3mm LED (red) for LED3 TxD 1 3mm LED (red) for LED3 TxD | | DigiKey DigiKey | 732-5006-ND 732-5006-ND | 0.17 0.17 | 5 5
1 1 | 1 75 Ω 1/8W resistor 1 75 Ω 1/8W resistor | | DigiKey DigiKey | CF18JT75R0CT-ND CF18JT75R0CT-ND | 0.10 0.10 | 5 5
1 1 | 1 220 Ω 1/8W resistor 1 220 Ω 1/8W resistor | | DigiKey DigiKey | CF18JT220RCT-ND CF18JT220RCT-ND | 0.10 0.10 | 5 5
1 1 | | 4.7K Ω 1/8W resistor 4.7K Ω 1/8W resistor | DigiKey DigiKey | CF18JT4K70CT-ND CF18JT4K70CT-ND | 0.10 0.10 | 5 5
1 1 | 1 10K Ω 1/8W resistor 1 10K Ω 1/8W resistor | | DigiKey DigiKey | CF18JT10K0CT-ND CF18JT10K0CT-ND | 0.10 0.10
2 2 | | TE/AMP 6-520314-5 FFC connector TE/AMP 6-520314-5 FFC connector | Heilind Heilind | 6-520314-5 6-520314-5 | 1.48 1.48 | 6 6
2 2 | | TE/AMP 6-520315-5 FFC connector TE/AMP 6-520315-5 FFC connector | Heilind Heilind | 6-520315-5 6-520315-5 | 1.48 1.48
1 1 | | 6” Flat flex cable, same side contacts 6” Flat flex cable, same side contacts | Wavelink Wavelink | 254-015-0155-AA 254-015-0155-AA | 10.00 10.00 | 7 7
1 1 | | 6” Flat flex cable, opposite side contacts 6” Flat flex cable, opposite side contacts | Wavelink Wavelink | 255-015-0155-AB 255-015-0155-AB | 10.00 10.00 | 7 7
1 1 | | Molex 22-27-2021 2-pin connector M Molex 22-27-2021 2-pin connector M | DigiKey DigiKey | WM4111-ND WM4111-ND | 0.27 0.27
1 1 | | Molex 22-01-3027 2-pin housing F Molex 22-01-3027 2-pin housing F | DigiKey DigiKey | WM2000-ND WM2000-ND | 0.12 0.12
1 1 | | Molex 22-27-2031 3-pin connector M Molex 22-27-2031 3-pin connector M | DigiKey DigiKey | WM4112-ND WM4112-ND | 0.35 0.35
1 1 | | Molex 22-01-3027 3-pin housing F Molex 22-01-3027 3-pin housing F | DigiKey DigiKey | WM2001-ND WM2001-ND | 0.18 0.18
4 4 | | Molex 08-50-0114 female pins tin Molex 08-50-0114 female pins tin | DigiKey DigiKey | WM1114-ND WM1114-ND | 0.78 0.78
3 3 | 1 1x2 header for J6,J7,J8 jumper 1 1x2 header for J6,J7,J8 jumper | | DigiKey DigiKey | 732-5315-ND 732-5315-ND | 0.39 0.39 | 8 8
3 3 | 1 Shorting jumper for J6,J7,J8 1 Shorting jumper for J6,J7,J8 | | DigiKey DigiKey | S9337-ND S9337-ND | 0.30 0.30 | 8 8
4 4 | | 3/16 x 3/8 female-male standoff 3/16 x 3/8 female-male standoff | DigiKey DigiKey | 1772-2032-ND 1772-2032-ND | 4.20 4.20
4 4 | | 0.28” diameter flat washer for #4-40 0.28” diameter flat washer for #4-40 | DigiKey DigiKey | 36-4692-ND 36-4692-ND | 0.33 0.33
4 4 | | Hex nut 3/16” #4-40 Hex nut 3/16” #4-40 | DigiKey DigiKey | 36-4694-ND 36-4694-ND | 0.30 0.30
4 4 | | #4-40 3/8” flat-head screw, phillips #4-40 3/8” flat-head screw, phillips | Bolt Depot Bolt Depot | 3717 3717 | 0.20 0.20
3 3 | | Self-tapping screws for bracket, clamp Self-tapping screws for bracket, clamp | Bolt Depot Bolt Depot | 7754 7754 | 0.15 0.15
1 1 | | Bracket to depress keyboard cables Bracket to depress keyboard cables | coat hanger coat hanger | | | 9 9
1 1 | | USB cable B panel to micro male, 24” USB cable B panel to micro male, 24” | DataPro DataPro | 1581-02C 1581-02C | 10.95 10.95
1 1 | | Cable clamp for USB cable Cable clamp for USB cable | DigiKey DigiKey | RP325-ND RP325-ND | 0.10 0.10
1 1 | | Cable tie Cable tie | DigiKey DigiKey | 298-1017-ND 298-1017-ND | 0.05 0.05
1 1 | 1 2x5 header, 4-wall, keyed 1 2x5 header, 4-wall, keyed | | DigiKey DigiKey | 3M155831-ND 3M155831-ND | 2.01 2.01
1 1 | 1 2x5 IDC ribbon cable socket 1 2x5 IDC ribbon cable socket | | DigiKey DigiKey | 3M156030-ND 3M156030-ND | 0.74 0.74
1 1 | 1 2x5 IDC strain relief 1 2x5 IDC strain relief | | DigiKey DigiKey | MESR10-ND MESR10-ND | 0.46 0.46
1 1 | 1 10-wire ribbon cable, 1 meter 1 10-wire ribbon cable, 1 meter | | DigiKey DigiKey | 732-11801-ND 732-11801-ND | 2.25 2.25 | 10 10
1 1 | 1 DE9-M panel mount IDC 1 DE9-M panel mount IDC | | DigiKey DigiKey | MMR09K-ND MMR09K-ND | 6.34 6.34
2 2 | 2 Jackscrew Socket with hardware 2 Jackscrew Socket with hardware | | DigiKey DigiKey | 160-17FA-ND 160-17FA-ND | 1.68 1.68
1 1 | 1 Solder lug for DE9 shield ground 1 Solder lug for DE9 shield ground | | DigiKey DigiKey | 36-7328-ND 36-7328-ND | 0.17 0.17 | 10 10
2 2 | | Hookup wire, red & black 24AWG, 8” Hookup wire, red & black 24AWG, 8” | DigiKey DigiKey | A2924R-100-ND A2924R-100-ND | 0.70 0.70 | 11 11
1 1 | | Set of ASCII keycaps Set of ASCII keycaps | Unicomp Unicomp | PSET 104+ (see note) PSET 104+ (see note) | 26.60 26.60 | 12 12
| | Total Total | | | 151.35 151.35 | 13 13

Parts List

Notes:
If the RS232 interface is not needed, reduce the part count by the number in the RS232 column.
1. Minimum order from OSH Park is three boards. Order at: https://oshpark.com/shared_projects/TIkAO4NE
2. Alternatively use Teensy 3.5 with pins plus two 24x1 sockets from PJRC.
3. Or alternates MAX3232EEPE+-ND, ADM3202ANZ-ND, SP3232E, MAX3232EPE+-ND
4. Only 9 capacitors are needed, but buy 10 for the price break.
5. Any LED color may be used, but may need a different resistor value for appropriate current and desired brightness. These were selected for similar appearance; 5mm LEDs may be substituted.
6. There may be no stock of this right-angle connector at the factory or any distributor, but the vertical connector 6-520315-5 can be modified for right-angle mounting, so buy four.
7. FFC cable sources in decreasing order of preference:
- Get custom order cables as listed, contact Chris Dobens, cdobens@wavelinkcable.com
- If not available, substitute 80 conductor 0.5mm pitch 150mm length FFC, one each with conductors on same and opposite sides, available, for example, on ebay in sets of five at https://www.ebay.com/itm/273811880007 and https://www.ebay.com/itm/372654797782
- Use latching connectors and cables per USB Interface Board Rev 1.6 BOM and instructions.
8. Fewer needed if you want to hardwire the terminal mode and/or enable of the RS232 LEDs.
9. Bend steel coat hanger wire using needle-nose pliers to form bracket per CAD diagram.
10. Alternatively use 9-wire ribbon cable 732-13985-ND if shell ground is not desired.
11. Minimum order is 100’ roll. Any hookup wire can be substituted.
12. Order the following keycaps at https://www.pckeyboard.com/page/category/Buttons:
- Complete Printed Buckling Spring Button Set, PSET 104 Pearl/Pebble – US
- Single Unit Key – Buckling Spring – printed, Pearl, characters “| \” (vertical bar, backslash)
- Single Unit Key – Buckling Spring – printed, Pearl, characters “Setup”
- Single Unit Key – Buckling Spring – unprinted
13. Shipping charges and taxes not included.
Tools Required
- phillips #0 and #1 screwdrivers
- large straight screwdriver
- 3/16” nut driver
- needle-nose pliers (may need two)
- diagonal cutters to clip PCB leads
- center punch and small hammer
- awl or ice pick
- IC insertion tool (optional)
- Xacto knife to cut Teensy trace
- soldering iron with fine tip
- desoldering tool or solder wick
- electric drill with 3/32”, 1/8” and countersink drill bits
- Dremel tool with cylindrical bit, or file, to shape holes in plastic back panel
- vise or water pump pliers to seat ribbon cable and covers on IDC connectors Materials
- masking tape
- double-stick tape
- scrap piece of 3/16” plywood or alternative

Notes:
If the RS232 interface is not needed, reduce the part count by the number in the RS232 column.
1. Minimum order from OSH Park is three boards. Order at: https://oshpark.com/shared_projects/TIkAO4NE
2. Alternatively use Teensy 3.5 with pins plus two 24x1 sockets from PJRC.
3. Or alternates MAX3232EEPE+-ND, ADM3202ANZ-ND, SP3232E, MAX3232EPE+-ND
4. Only 9 capacitors are needed, but buy 10 for the price break.
5. Any LED color may be used, but may need a different resistor value for appropriate current and desired brightness. These were selected for similar appearance; 5mm LEDs may be substituted.
6. There may be no stock of this right-angle connector at the factory or any distributor, but the vertical connector 6-520315-5 can be modified for right-angle mounting, so buy four.
7. FFC cable sources in decreasing order of preference:
- Get custom order cables as listed, contact Chris Dobens, cdobens@wavelinkcable.com
- If not available, substitute 80 conductor 0.5mm pitch 150mm length FFC, one each with conductors on same and opposite sides, available, for example, on ebay in sets of five at https://www.ebay.com/itm/273811880007 and https://www.ebay.com/itm/372654797782
- Use latching connectors and cables per USB Interface Board Rev 1.6 BOM and instructions.
8. Fewer needed if you want to hardwire the terminal mode and/or enable of the RS232 LEDs.
9. Bend steel coat hanger wire using needle-nose pliers to form bracket per CAD diagram.
10. Alternatively use 9-wire ribbon cable 732-13985-ND if shell ground is not desired.
11. Minimum order is 100’ roll. Any hookup wire can be substituted.
12. Order the following keycaps at https://www.pckeyboard.com/page/category/Buttons:
- Complete Printed Buckling Spring Button Set, PSET 104 Pearl/Pebble – US
- Single Unit Key – Buckling Spring – printed, Pearl, characters “| \” (vertical bar, backslash)
- Single Unit Key – Buckling Spring – printed, Pearl, characters “Setup”
- Single Unit Key – Buckling Spring – unprinted
13. Shipping charges and taxes not included.
Tools Required
- phillips #0 and #1 screwdrivers
- large straight screwdriver
- 3/16” nut driver
- needle-nose pliers (may need two)
- diagonal cutters to clip PCB leads
- center punch and small hammer
- awl or ice pick
- IC insertion tool (optional)
- Xacto knife to cut Teensy trace
- soldering iron with fine tip
- desoldering tool or solder wick
- electric drill with 3/32”, 1/8” and countersink drill bits
- Dremel tool with cylindrical bit, or file, to shape holes in plastic back panel
- vise or water pump pliers to seat ribbon cable and covers on IDC connectors Materials
- masking tape
- double-stick tape
- scrap piece of 3/16” plywood or alternative


USB & RS232 Interface Board Rev. 2.0 Schematic

Modified Wheelwriter CAD Diagram
To see details in this diagram more clearly, try viewing the PDF file for this document online and zoom in. Better yet, view the original PDF of this diagram with black background and scalable graphics that is downloadable from:

https://github.com/IBM-1620/ (https://github.com/IBM-1620/Cadetwriter/raw/master/docs/adaptation_guide/wheelwriter-adaptation-CAD.pdf) Cadetwriter (https://github.com/IBM-1620/Cadetwriter/raw/master/docs/adaptation_guide/wheelwriter-adaptation-CAD.pdf) /raw/master/docs/ (https://github.com/IBM-1620/Cadetwriter/raw/master/docs/adaptation_guide/wheelwriter-adaptation-CAD.pdf) adaptation_guide/ (https://github.com/IBM-1620/Cadetwriter/raw/master/docs/adaptation_guide/wheelwriter-adaptation-CAD.pdf)wheelwriter-adaptation-CAD.pdf (https://github.com/IBM-1620/Cadetwriter/raw/master/docs/adaptation_guide/wheelwriter-adaptation-CAD.pdf)

Modified Wheelwriter CAD Diagram
To see details in this diagram more clearly, try viewing the PDF file for this document online and zoom in. Better yet, view the original PDF of this diagram with black background and scalable graphics that is downloadable from:

https://github.com/IBM-1620/ (https://github.com/IBM-1620/Cadetwriter/raw/master/docs/adaptation_guide/wheelwriter-adaptation-CAD.pdf) Cadetwriter (https://github.com/IBM-1620/Cadetwriter/raw/master/docs/adaptation_guide/wheelwriter-adaptation-CAD.pdf) /raw/master/docs/ (https://github.com/IBM-1620/Cadetwriter/raw/master/docs/adaptation_guide/wheelwriter-adaptation-CAD.pdf) adaptation_guide/ (https://github.com/IBM-1620/Cadetwriter/raw/master/docs/adaptation_guide/wheelwriter-adaptation-CAD.pdf)wheelwriter-adaptation-CAD.pdf (https://github.com/IBM-1620/Cadetwriter/raw/master/docs/adaptation_guide/wheelwriter-adaptation-CAD.pdf)


Templates
Print and cut out these templates for use during the Wheelwriter modification procedures. Verify that the printer scaling is accurate by measuring the dimensions (in inches) as shown on the Wheelwriter USB & RS232 Interface Template which shows where to drill mounting holes for the board.


The second template is for drilling and cutting holes in the knockout panel at the rear of the Wheelwriter base for mounting the USB-B cable and RS232 cable. The black lines indicate the size of the cutouts while the red lines indicate the size of the connector bodies behind the panel.

Two variants are provided; the first shares one screw between the two
connectors by overlapping the flange of the DE-9 connector on the
outside of the panel with the ear of the USB-B connector behind the
panel. The red lines indicate interference between rear bodies of the two connectors, but there is enough slop in the holes to allow the connectors to fit. To ease the fit, use a file or knife to shave about 1/32” off the
plastic surrounding the captive nut in the USB-B connector. This
arrangement works since the USB plug is narrow, as shown in the photo.


The second variant uses separate screws for the two connectors but leaves only a narrow section of the plastic panel to the right of the DE-9 connector and creates a rather tight space between the two connectors for getting in a tool to hold the nut. The distance between the mounting holes for the USB-B connector is 26 mm (1.024 inches) and for the DE-9 connector is 0.98 inches.

Templates
Print and cut out these templates for use during the Wheelwriter modification procedures. Verify that the printer scaling is accurate by measuring the dimensions (in inches) as shown on the Wheelwriter USB & RS232 Interface Template which shows where to drill mounting holes for the board.

The second template is for drilling and cutting holes in the knockout panel at the rear of the Wheelwriter base for mounting the USB-B cable and RS232 cable. The black lines indicate the size of the cutouts while the red lines indicate the size of the connector bodies behind the panel.

Two variants are provided; the first shares one screw between the two
connectors by overlapping the flange of the DE-9 connector on the
outside of the panel with the ear of the USB-B connector behind the
panel. The red lines indicate interference between rear bodies of the two connectors, but there is enough slop in the holes to allow the connectors to fit. To ease the fit, use a file or knife to shave about 1/32” off the
plastic surrounding the captive nut in the USB-B connector. This
arrangement works since the USB plug is narrow, as shown in the photo.

The second variant uses separate screws for the two connectors but leaves only a narrow section of the plastic panel to the right of the DE-9 connector and creates a rather tight space between the two connectors for getting in a tool to hold the nut. The distance between the mounting holes for the USB-B connector is 26 mm (1.024 inches) and for the DE-9 connector is 0.98 inches.


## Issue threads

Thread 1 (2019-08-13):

Digikey PN for 4.7K resistor is wrong

MustBeArt, 2019-08-13:
In the adaptation instructions, in the parts list, the DigiKey part number for the 4.7K resistor is the same as the part number for the 10K resistor. It should be CF18JT4K70CT-ND I think.

slcasner, 2019-08-13:
Thanks for the bug report.  Fixed in 1d15698cf423c813fa3d037a9fa6028c2801185e

Closed 2019-08-13.

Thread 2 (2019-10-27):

Auto paper load doesn't work

MustBeArt, 2019-10-27:
The unmodified Wheelwriter 1000 has a semi-automatic paper loading feature. You pull back on the Paper Bail Load Lever and the paper is automatically fed into the machine and advanced to the top margin. This does not happen with the Cadetwriter board installed, even when configured for Standalone Typewriter mode.

Problem confirmed by Dave Babcock.

DaveB1620, 2019-11-11:
Problem fixed in firmware version 5R5 for all emulations.  The semi-automatic paper loading feature now works with a standard serial interface board and one modified as described in the Cadetwriter building channel (https://cadetwriter.slack.com).  Fix verified by submitter.

Closed 2019-11-11.

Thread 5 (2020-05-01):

HW Flow control doesn't seem to work.

zaphodbe, 2020-05-01:
Looking through the code I can't find anything that operates when hwflow is set to HWFLOW_RTS_CTS as such the pin is set high in Setup_ASCII and then never gets changed.

DaveB1620, 2020-05-02:
Chris is correct, HW flow control isn't correctly implemented.  It will be fixed in the next update.

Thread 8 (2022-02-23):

Confusion about the wavelink cable

twiclo, 2022-02-23:
Can you please be more specific about the type of cable needed from wavelink? Digikey has many flex cables so if it's possible I'd like to see if I can get it from digikey

slcasner, 2022-02-23:
On Tue, 22 Feb 2022, Tanner Wilcox wrote:

> Can you please be more specific about the type of cable needed from
> wavelink? Digikey has many flex cables so if it's possible I'd like
> to see if I can get it from digikey

The part numbers for the Wavelink cables are shown in the Parts List
of the wheelwriter-adaptation-instructions.pdf guide: 254-015-0155-AA
and 254-015-0155-AB, with same side and opposite side contacts,
respectively.  These are flat flex cables with no connectors on the
ends, they just have the plastic covering cut away to expose the
traces that are then plated.  These cables fit nicely into the
existing connectors on the Wheelwriter logic board.

The Digikey cables have a latching plastic connector on the end.  We
used those for our first prototype, but that required removing (and
harvesting) the connectors from the Wheelwriter logic board to move
them to the serial interface board.  That is not easy and risks damage
to the logic board.

Our updated design uses the Wavelink cables together with the same
type of ZIF connectors that are on the logic board.  This was enabled
after we finally found a source for those connectors -- Heilind.  But
I bought 50 of them just in case they stopped being available.  I can
send four of them to you for $1 each plus USPS shipping if you like.

                                                        -- Steve

twiclo, 2022-02-23:
I appreciate the offer but maybe we can find a product on digikey and future visitors won't have to rely on an out of production cable. I'm wondering why I can't buy the cable off digikey and remove the connector myself.  Or maybe I can buy something like this?

slcasner, 2022-02-23:
Are you saying that Wavelink no longer has any stock?  They agreed to make 25 sets for me on speculation, and I have been concerned that there would not be enough takers.

twiclo, 2022-02-23:
I haven't contacted WaveLink yet. I'll go through them or you to get the cable I'm only asking what the difference is between these wavelink cables and the one I posted. Wouldn't it be better if these cables could be included in the order everyone who does this has to make on digikey?

slcasner, 2022-02-23:
The specific cable you referenced is not wide enough and is so long it would get in the way.  I did test some 80-conductor 0.5mm pitch 150mm length FFC cables that I found on ebay, figuring that at least one of the conductors would contact the pin in the connector.  I was able to get them to work in the Wheelwriter 1000 but they are not as thick/firm so it was harder to push them into the connectors.
 but not in the Wheelwriter Model 30 Series II because that logic board uses a true ZIF connector (zero rather than just low insertion force) with a latch where the metal of the pin is perpendicular to the cable surface and therefore touches only a narrow edge.  But you would still need the connectors from Heilind, so the order would not all come from Digikey.
You also asked about buying the Digikey cables with latching connectors and removing the connectors on the ends mating with the logic board.  Chopping off the connector and then peeling back the plastic cover would be difficult to do without damaging the copper conductors, and then the unplated copper would tend to oxidize over time (the Wavelink cables have gold platiing).  You would also need to attach a stiffener to the back side.
I strongly suggest that your best course of action would be to buy the cables from Wavelink.

twiclo, 2022-02-23:
Fair enough. I'll contact them and follow up if they're unable to provide me with the cable

twiclo, 2022-02-23:
Actually can I take you up on your offer? They want $25 per cable

slcasner, 2022-02-23:
Hmm, that is a jump from the $15 they quoted before, but I think still not unreasonable.  When we were trying to find a source for cables to fit the logic board, the other vendors who could make them wanted $1000 setup cost for a run since this dimensions of these cables are outdated.

My offer was for the FFC connectors (TE/AMP 6-520315-5) that you otherwise need to get from Heilind since I bought 50 of them.  I don't have the FFC cables to sell.

twiclo, 2022-03-30:
I'm finally getting around to ordering parts for the conversion and would like to take you up on the offer for those connectors. Can you please shoot me an email so we can coordinate: tanner@twil.cx

slcasner, 2022-03-30:
Email sent.

Closed 2022-02-23.

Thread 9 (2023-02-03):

Board revision not reliably detected by firmware

Neukam, 2023-02-03:
I've been testing the Cadetwriter interface on my Personal Wheelwriter 2 over the last few days and have been experiencing some very strange behavior after power on, and extra erroneous characters being printed when the requested character is not on row 4.  I have finally tracked down the cause, and a solution.

The issue is related to the fact that the firmware supports different revisions of the hardware with different functions for certain pins.  Upon startup and during initialization, the firmware reads the state of pin 33 (PTE24), which is the output for the blue LED.  If the pin is high, the firmware assumes the board is v1.6 or v1.7.  If the pin is low, the firmware assumes the board is v2.0.  The pin functions are then set according to that determination.  The problem with this is that the forward voltage drop of the blue LED is too great and the board revision is not always determined correctly.  When the board revision is incorrectly determined, the functions for RTS, CTS, ROW_OUT_3 AND ROW_OUT_4 are incorrectly set, causing the strange behavior.

My solution to the problem is to install a 10k pulldown resistor between pin 33 (PTE24) and ground.  This will ensure that the firmware properly reads the state of that pin as low during initialization, and properly sets the board revision.  This will not interfere with the operation of the LED and will work properly with the existing firmware.  I installed the resistor on the back of the board as shown.  This has restored correct, reliable operation to the Cadetwriter.

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

DaveB1620, 2023-02-15:
Mike,

Great work!

Thank you for sharing your solution to this problem.  I haven't heard of
anyone else having an issue with this, but if someone does, your fix is
a good option for them.

If someone doesn't want to make a hardware change, a simple modification
to the software could be made to hard-code.

Thanks,
Dave

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

Neukam, 2023-02-15:
Dave,

There were a couple users on the Slack forum that were experiencing very similar if not identical behavior, although their problems seemed to clear up inexplicably, seemingly indicating a poor connection to be the cause.  I can’t help but wonder if they are still having intermittent problems.  Hard coding the board revision is certainly not a bad solution, but the hardware fix allows people to use the precompiled binaries regardless of the board revision.  I don’t know how many of the early rev boards are in use, so I didn’t want to do anything that would break compatibility with the early boards.  If there are only a handful of early boards, then it might be worthwhile to hard code it for future releases.  If there are a relatively large number of early boards, then I’d recommend the hardware fix for boards that need it, to maintain a single common firmware.  Either way, I would recommend that the issue be noted somewhere in the documentation.  I thought the detection routine was rather clever, but the use of a blue LED in the circuit brings it right to the threshold where it may not work reliably.

By the way, I also modified the keyboard on my Wheelwriter to add the pipe/backslash key above the enter key.  I posted some info about it on the Slack forum.  If you haven’t seen it, you might want to check it out.

Mike Neukam

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

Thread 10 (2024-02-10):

Teensy 3.5 no longer available

jdmarble, 2024-02-10:
It's out of stock at all of the distributors I know. PJRC made a final, small batch on August 15, 2023 and are now out. They recommend migrating to the Teensy 4.1 which looks similar physically and electrically, except it isn't 5v tolerant. Has anyone tried the Teensy 4.1?

HK8088, 2024-03-11:
is there any solution to this? potentially use level shifters on the inputs?

TheHarvard, 2025-05-21:
This is what is stopping me from trying this project as well - I'm half tempted to try to bodge in a voltage level shifter, but that is the kind of engineering naiveté that get's me into months long tangents and broken hardware.

DaveB1620, 2025-05-22:
Chris,I think that it would still be beneficial to have a Teensy 4.1 version.Thanks,DaveOn May 21, 2025, at 11:23 AM, Chris Coley ***@***.***> wrote:
zaphodbe left a comment (IBM-1620/Cadetwriter#10)
I started looking at alternatives to the 3.5, but got side tracked with other work.  If there is serious interest I'll take another look.

—Reply to this email directly, view it on GitHub, or unsubscribe.You are receiving this because you are subscribed to this thread.Message ID: ***@***.***>

DaveB1620, 2025-06-12:
Håvard - please send me private email (cadetwriter at ibm1620.org).  I may have another option for you.  Thanks, Dave

HK8088, 2025-06-16:
Could I know about this other option?

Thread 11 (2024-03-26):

Possible to adapt to wheelwriter II?

sirus20x6, 2024-03-26:
Was looking at purchasing a wheelwriter 7000, but I just got a wheelwriter II from work. is it possible to convert this to work with the WW2? I do circuit board design and programming for a living so I have no problem with making changes, I just haven't taken a look at the internals of any wheelwriter yet.

zaphodbe, 2024-03-26:
Don't know about the wheelwriter II.  But most of them are very similar, so
as long as the keyboard interface is the same it should work although
tuning may be necessary.  I have done both a 1000 and a 1500 although the
1500 was a little harder to fit the board in.

Recently there were some recent grumblings over availability of the
teensyduino that is used.  So this may be an issue for you.

Chris

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

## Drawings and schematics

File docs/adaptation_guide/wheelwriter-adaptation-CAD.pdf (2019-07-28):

# IBM 1620 Jr. Project Wheelwriter Adaptation

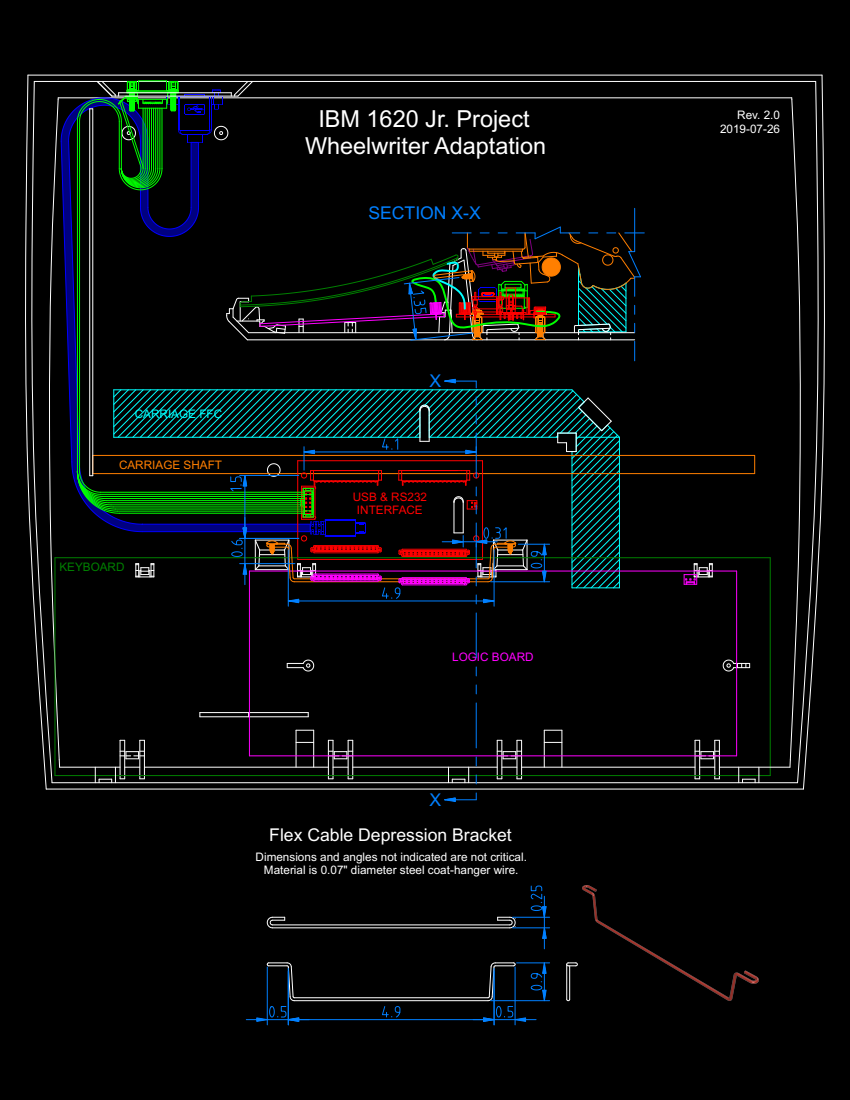
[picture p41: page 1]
CARRIAGE SHAFT; CARRIAGE FFC; KEYBOARD; USB & RS232 INTERFACE; LOGIC BOARD; Rev. 2.0 2019-07-26; SECTION X-X

Flex Cable Depression Bracket

Dimensions and angles not indicated are not critical. Material is 0.07" diameter steel coat-hanger wire.

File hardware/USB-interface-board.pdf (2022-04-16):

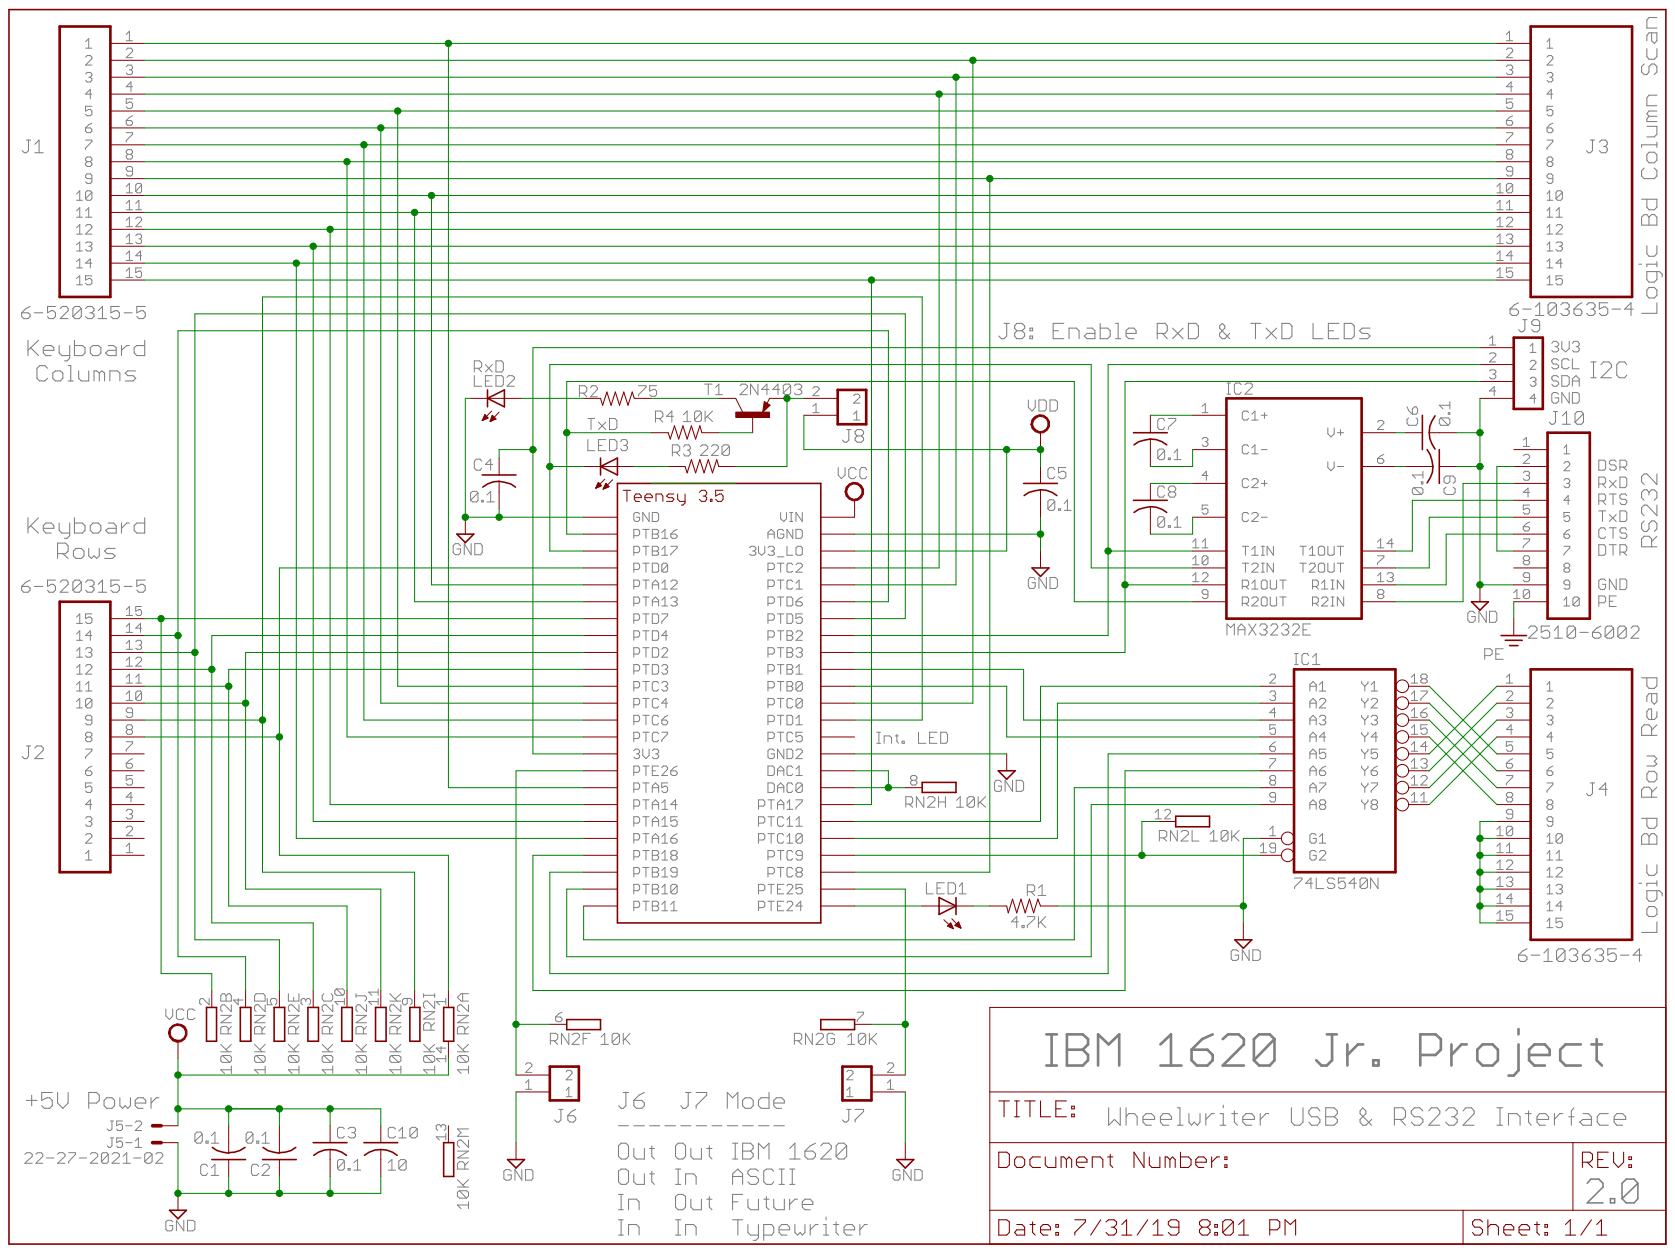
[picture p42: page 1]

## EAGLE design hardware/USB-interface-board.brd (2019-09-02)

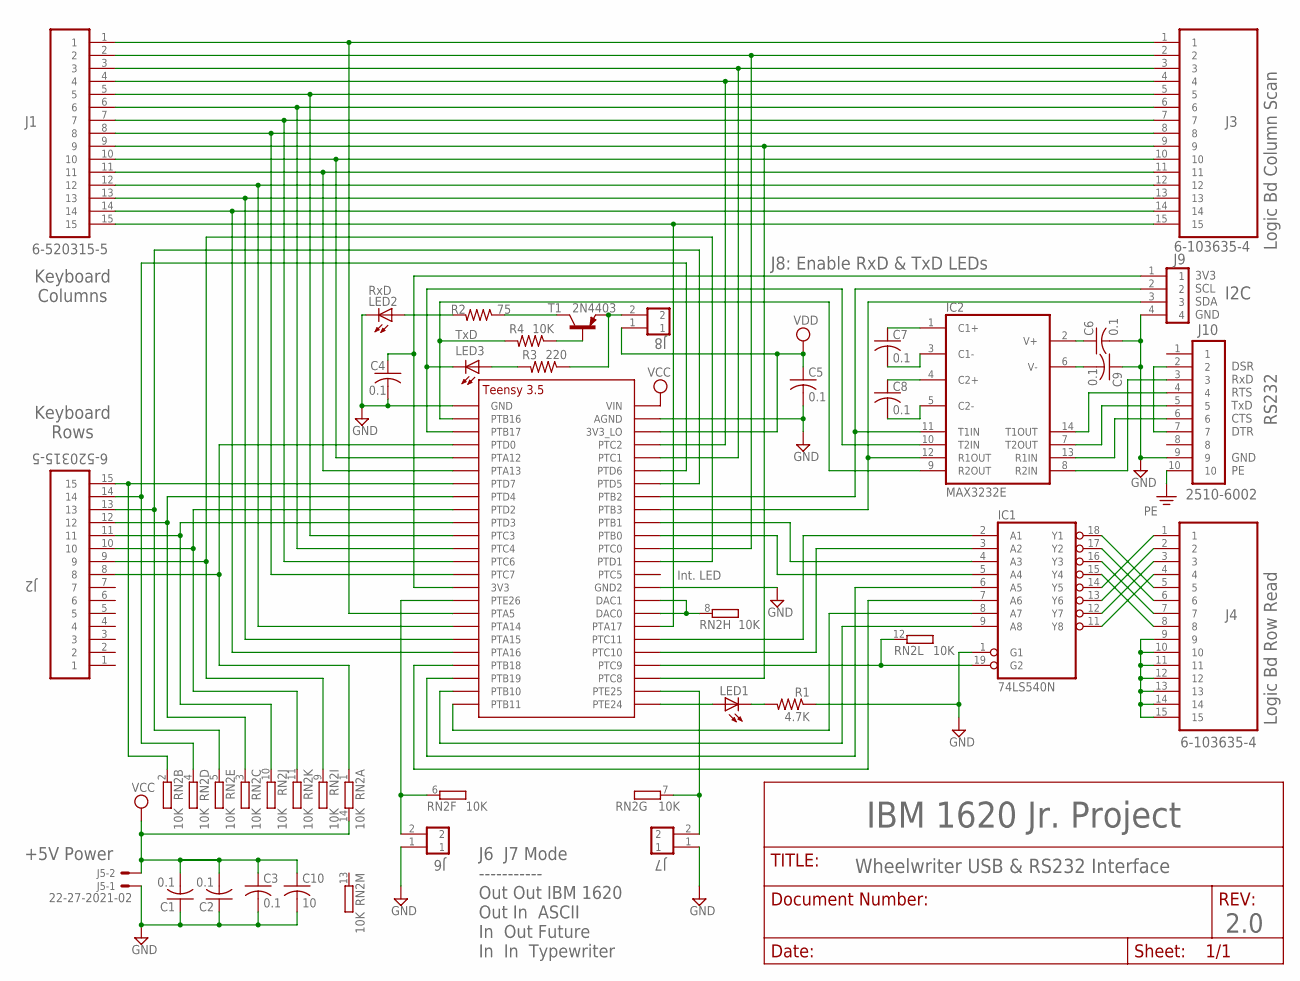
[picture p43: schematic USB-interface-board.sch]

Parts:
C1, C2, C3, C4, C5, C6, C7, C8, C9: 0.1; C025-025X050
C10: 10; C050-035X075
IC1: 74LS540N; DIL20
IC2: MAX3232E; DIL16
J1: 6-520315-5
J2: 6-520315-5; 6-520315-5-U
J3, J4: 6-103635-4
J5: 22-27-2021-02; 6410-02
J6, J7, J8: HEADER-1X2
J9: HEADER-1X4
J10: 2510-6002; PAK100/2500-10
LED1: LED3MM
LED2: RxD; LED3MM
LED3: TxD; LED3MM
R1: 4.7K; 0204/5
R2: 75; 0204/5
R3: 220; 0204/5
R4: 10K; 0204/5
RN2: 10K; DIL14
T1: 2N4403; TO92
U$1: TEENSY_3.5_BASIC

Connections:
GND: C1.1, C2.1, C3.2, C4.2, C5.2, C6.2, C9.1, C10.2, IC1.1 (G1), IC1.10 (GND), IC2.15 (GND), J5.1, J6.1, J7.1, J9.4, J10.9, LED2.K (C), R1.1, U$1.AGND, U$1.GND, U$1.GND2
unnamed: J1.2, J3.2, U$1.PTC0
unnamed: J1.3, J3.3, U$1.PTC1
unnamed: J1.4, J3.4, U$1.PTC2
unnamed: J1.5, J3.5, U$1.PTC3
unnamed: J1.6, J3.6, U$1.PTC4
unnamed: J1.7, J3.7, U$1.PTC6
unnamed: J1.8, J3.8, U$1.PTC7
unnamed: J1.9, J3.9, U$1.PTC8
unnamed: J1.10, J3.10, U$1.PTA12
unnamed: J1.11, J3.11, U$1.PTA13
unnamed: J1.12, J3.12, U$1.PTA14
unnamed: J1.13, J3.13, U$1.PTA15
unnamed: J1.14, J3.14, U$1.PTA16
unnamed: J1.15, J3.15, U$1.PTA17
unnamed: J2.15, RN2.2 (1), U$1.PTD7
unnamed: J2.14, RN2.4 (1), U$1.PTD6
unnamed: J2.13, RN2.5 (1), U$1.PTD5
unnamed: J2.12, RN2.3 (1), U$1.PTD4
unnamed: J2.11, RN2.10 (1), U$1.PTD3
unnamed: J2.10, RN2.11 (1), U$1.PTD2
unnamed: J2.9, RN2.9 (1), U$1.PTD1
unnamed: J2.8, RN2.1, U$1.PTD0
unnamed: IC1.11 (Y8), J4.4
unnamed: IC1.12 (Y7), J4.3
unnamed: IC1.13 (Y6), J4.2
unnamed: IC1.14 (Y5), J4.1
unnamed: IC1.15 (Y4), J4.8
unnamed: IC1.16 (Y3), J4.7
unnamed: IC1.17 (Y2), J4.6
unnamed: IC1.18 (Y1), J4.5
unnamed: J4.9, J4.10, J4.11, J4.12, J4.13, J4.14, J4.15
unnamed: IC1.8 (A7), U$1.PTB11
unnamed: IC1.9 (A8), U$1.PTB10
unnamed: IC1.6 (A5), U$1.PTB19
unnamed: IC1.7 (A6), U$1.PTB18
unnamed: IC1.5 (A4), U$1.PTB0
unnamed: IC1.4 (A3), U$1.PTB1
unnamed: IC1.2 (A1), U$1.PTC11
unnamed: IC1.3 (A2), U$1.PTC10
unnamed: J6.2, RN2.6 (1), U$1.PTE26
unnamed: C6.1, IC2.2 (V+)
unnamed: LED1.K (C), R1.2
unnamed: LED1.A, U$1.PTE24
unnamed: J7.2, RN2.7 (1), U$1.PTE25
unnamed: C9.2, IC2.6 (V-)
unnamed: IC2.14 (T1OUT), J10.4
unnamed: C4.1, J9.1, U$1.3V3
unnamed: IC2.12 (R1OUT), J9.3, U$1.PTB3
unnamed: C7.1, IC2.1 (C1+)
unnamed: J10.2, J10.7
unnamed: IC1.19 (G2), RN2.12 (1), U$1.PTC9
unnamed: J1.1, J3.1, U$1.PTA5
unnamed: C7.2, IC2.3 (C1-)
unnamed: C8.1, IC2.4 (C2+)
unnamed: C8.2, IC2.5 (C2-)
unnamed: IC2.11 (T1IN), J9.2, U$1.PTB2
unnamed: IC2.9 (R2OUT), R4.2, U$1.PTB16
unnamed: IC2.10 (T2IN), LED3.K (C), U$1.PTB17
unnamed: IC2.7 (T2OUT), J10.5
unnamed: IC2.8 (R2IN), J10.3
unnamed: IC2.13 (R1IN), J10.6
unnamed: R2.1, T1.1 (C)
unnamed: LED3.A, R3.2
unnamed: LED2.A, R2.2
unnamed: RN2.8 (1), U$1.DAC0, U$1.DAC1
unnamed: J8.2, R3.1, T1.3 (E)
unnamed: R4.1, T1.2 (B)
PE: J10.10
VCC: C1.2, C2.2, C3.1, C10.1, IC1.20 (VCC), J5.2, RN2.14 (2), U$1.VIN
VDD: C5.1, IC2.16 (VDD), J8.1, U$1.3V3_LO

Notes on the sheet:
2.0
IBM 1620 Jr. Project
Int. LED
Wheelwriter USB & RS232 Interface
J8: Enable RxD & TxD LEDs
J6 J7 Mode ----------- Out Out IBM 1620 Out In ASCII In Out Future In In Typewriter
Keyboard Columns
Keyboard Rows
Logic Bd Column Scan
Logic Bd Row Read
3V3 SCL SDA GND
I2C
+5V Power
DSR RxD RTS TxD CTS DTR GND PE
RS232

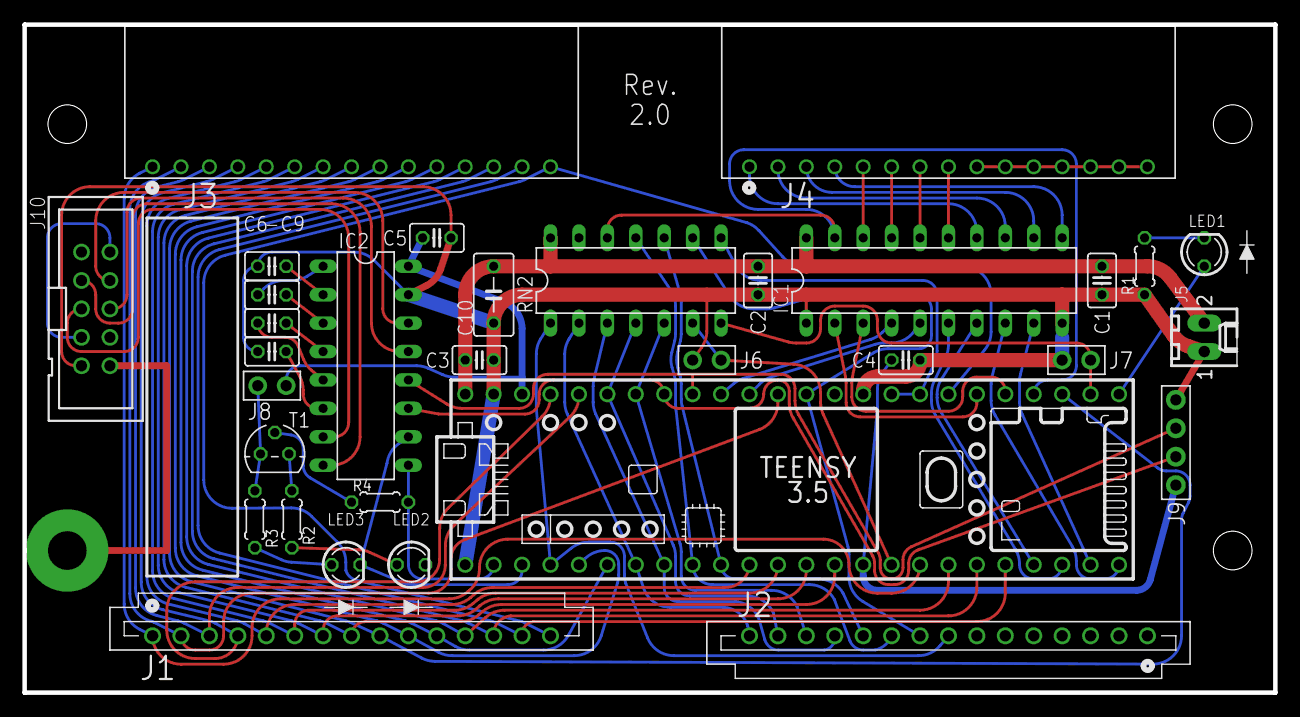
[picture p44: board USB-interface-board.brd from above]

Board: 2 copper layers, 111.8 x 59.7 mm, 35 parts (0 on the bottom side), 70 nets.

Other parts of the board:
U$2, U$4, U$5: MOUNTING_HOLE

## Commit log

2019-07-10 Update file permission on keyboard_matrix.xlsx
    [keyboard_matrix.xlsx]
2019-07-10 Update file permission on teensy_pin_assignments.xls
    [teensy_pin_assignments.xlsx]
2019-07-28 Add Rev. 2.0 version of CAD diagram
2019-07-28 Enlarge scale of CAD diagram to fill the page
2019-08-12 Update available baud rate due to limitation of Teensy 3.5.
2019-08-13 Cleaned up printed ASCII character set.
2019-08-13 Correct part number for 4.7K resistor
2019-09-02 Replace PNG diagrams with SVG and add appendix for latching connectors
    1. The schematic diagram and the CAD diagram are updated now to use
    SVG graphics rather than PNG raster images. This allows full
    resolution when zooming in on those diagrams in the PDF rendering of
    the document.
    2. Rather than referring to the earlier adaptation instructions for
    the Rev. 1.6 board, now the alternate instruction for using FFC cables
    with latching connectors is added as a one-page appendix.
2019-09-02 Add EAGLE CAD files for USB & RS232 Interface Board
    [USB-interface-board.brd, USB-interface-board.sch]
2019-09-02 Add gerber files for USB & RS232 Interface Board
2019-11-12 Latest version of keyboard matrix.
    [keyboard_matrix.xlsx]
2019-11-19 Update price and contact information for Wavelink FFC cables. Remove extra blank page at the end.
2020-02-12 Update parts list
    1. Substitute an ROHS variant part for the 2x5 header, 4-wall, keyed
    that is about to be end-of-life.
    2. Revise the FFC cable sources to remove the 80-conductor cable
    alternative since Wavelink has made a production run of the proper
    15-conductor cables.
2020-05-13 Added Wheelwriter 1500 to keyboard_matrix.xls. [Thanks to Chris Coley.] Added wheelwriter_1500_user_manual.pdf. [ " ]
    [keyboard_matrix.xlsx]
2020-05-14 Added Wheelwriter 30 Series II User Manual.
2020-05-15 Added more Wheelwriter User Manuals.
2020-05-16 Added print sample for each machine.
    [keyboard_matrix.xlsx]
2020-05-23 Updated keyboard matrix spreadsheet with Wheelwriter 1500. Added ISO/IEC escape sequence documentation. Added Paul Williamson's 3D-printable paper guide.
    [escape_sequences.xlsx, keyboard_matrix.xlsx]
2020-11-29 Serial_Interface_Board.ino revision 5R10. - Corrected RS-232 hardware flow control. - Fixed a problem with software flow control. - Switched sense of flow_in_on and flow_out_on to be more consistent.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
    [keyboard_matrix.xlsx]
2021-02-17 Added ASCII printwheel character set and printwheel character ordering.
    [keyboard_matrix.xlsx]
2021-02-20 Correct typo.
    [keyboard_matrix.xlsx]
2021-02-27 Added more printwheel information.
    [keyboard_matrix.xlsx]
2021-03-14 Updated IBM 1620 Max keyboard layout.
    [keyboard_matrix.xlsx]
2021-03-14 Corrected printwheel data.
    [keyboard_matrix.xlsx]
2021-03-15 Added Operations page.
    [keyboard_matrix.xlsx]
2021-03-18 Corrected mapping of margin and tab control keys.
    [keyboard_matrix.xlsx]
2021-04-26 Major update to firmware (version 6R0) with these changes: Developed new Spin-Hit-Move (SHM) printer timing model. Added developer column scan timing measurements and rewrote printer timing. Added co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
    Public release of the Cadetwriter User Guide.
2021-07-29 Found more Wheelwriter manuals.
2022-04-16 Add PDF version of the schematic to allow viewing without opening in the EAGLE CAD app.
